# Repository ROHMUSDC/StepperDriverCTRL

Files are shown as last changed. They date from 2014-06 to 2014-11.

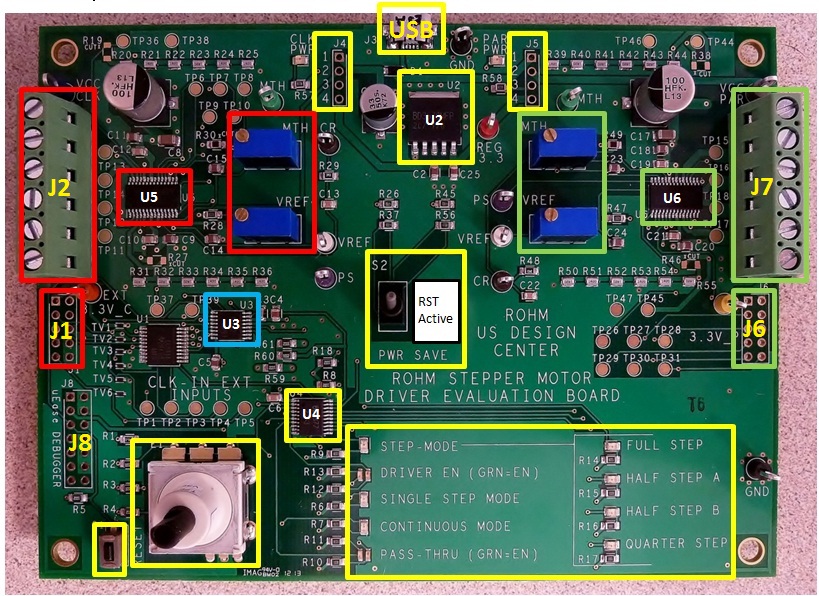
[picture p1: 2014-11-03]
raw images for manual/Fig 02 - Stepper Eval Board Diagram (labled).jpg

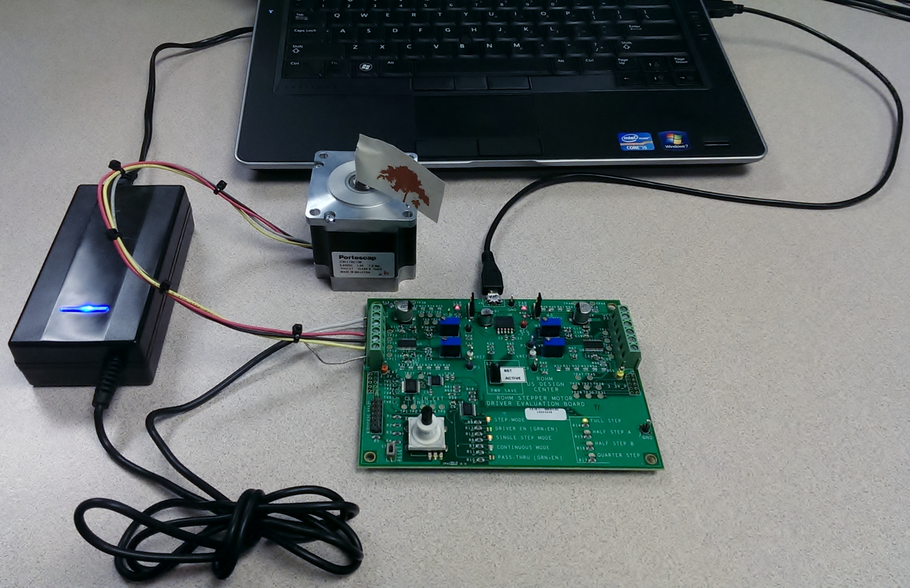
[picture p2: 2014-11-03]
raw images for manual/Fig 06 - Example Test Setup.jpg

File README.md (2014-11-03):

StepperDriverCTRL
=================

MCU: Lapis ML610Q102

The fully commented CONTROL firmware in this file is used to drive the ROHM BD63720EFV Stepper Motor Driver Eval Board. It is intended for reference. There are also many additional support files on this site. These support files for the for the Stepper Motor Eval Board include the Full User Manual a getting Started Flyer, Schematics, Bill of Material, etc.

This is the release version...but I do have plans to make future improvements...such as improving Continuous mode.

Evaluation Board Objective To allow customers and applications support the ability to evaluate any of Rohm’s BD637xx High Performance and BD638xx Micro Stepping Motor Drivers in a quick and easy environment. This document will describe the operation and functionality of the evaluation board.

Functionality The evaluation board has two drivers installed, the ROHM BD63720 Clock-in and the ROHM BD63876 Parallel input type. The BD63720 clock-driven High Performance Stepper Motor Driver is connected to an on-board LAPIS micro (ML610Q102) for demonstration purposes. Each circuit can also be connected to a user’s external MCU to control the driver and operate the attached stepper motor. Additionally, the ROHM BD63720 circuit can be controlled manually in a single step or continuous mode. The ROHM BD63720 and ROHM BD63876 are the 2A versions of each type. Users of lower current devices will be able to use these for evaluation as well.

Getting to know your Stepper Motor Eval Board • The RED Blocks in the Picture above highlight the key portions of the ROHM BD63720 Clock-in Stepper Motor Driver LSI (U5). The green terminal Block (J2) is where you will add Power for the Stepper Motor (i.e.: 24Vdc & GND), as well as where you will connect the 4 legs of the Bi Polar Stepper Motor windings if you want this IC to drive the Motor. This motor driver LSI is designed to be controlled via on-board pre-programmed Lapis ML610Q102 mcu (Blue Box above) (U3), or able to control via external mcu provided by the user (J1) • The Green Blocks in the Picture above highlight the key portions of the ROHM BD63876 Parallel-in Stepper Motor Driver LSI (U6). The green terminal Block (J7) is where you will add Power for the Stepper Motor (i.e.: 24Vdc & GND), as well as where you will connect the 4 legs of the Bi Polar Stepper Motor windings if you want this IC to drive the Motor. This motor driver LSI is designed to be controlled only via external mcu provided by the user (J6)

• The ROHM (SML-21 Series) LED’s in the lower corner of the board are controlled via a ROHM BD8377 12-ch. LED Driver (U4), and are used to indicate which Machine State the eval board in currently in in (adjustable via the push button encoder knob (E1)): o 4 possible Step Modes (Full, Half-A, Half-B or Quarter Step) o 2 possible Driver States (Disabled or Enabled) o 2 Possible Operation Modes (Single-Step or Continuous Mode) o 2 Possible Pass-Thru States (Disabled or Enabled)

• Suggested Motor o Portescap 23H118D10B Stepper Motor (1.8 Deg Step Angle; BiPolar) o Availible at DigiKey: http://www.digikey.com/product-detail/en/23H118D10B/403-1039-ND/1894182

• Key Potentiometer & Switch Settings o MTH => Current decay mode setting terminal (SLOW, MIXED or FAST Decay) o VREF => Output current value setting terminal o CR => Terminal to set the Chopping Frequency of output o PS => Power Save terminal - can put circuit in standby mode state and allow motor _ to operate o J4 & J5 => Both should jump pins 3 & 4 together to allow powering control circuitry (3.3V) on the eval board from the power provided in the USB connector (5V) which is regulated down to 3.3V via the ROHM BD3570HFP LDO Voltage Regulator (U2).

Evaluation Board Objective To allow customers and applications support the ability to evaluate any of Rohm’s BD63720 & BD63876 High Performance Stepping Motor Drivers in a quick and easy environment.

Functionality The evaluation board has two drivers installed, the BD63720 Clock-in and the BD63876 Parallel input type. Each circuit can be connected to a user’s MCU to control the driver and operate the attached stepper motor. Additionally, the BD63720 circuit can be controlled manually in a single step or continuous mode.

LED INDICATORS • Step Mode Indicates that the step modes can be selected by rotating the knob. o Full Step Indicates that the Full Step Mode has been selected for manual mode o Half Step A Indicates that the Half Step A Mode has been selected for manual mode. o Half Step B Indicates that the Half Step B Mode has been selected for manual mode. o Quarter Step Indicates that the Quarter Step Mode has been selected for manual mode. • Driver Enabled - RED Indicates that the Manual mode is ready but currently disabled • Driver Enabled - GREEN Indicates that the driver is now enabled for Manual mode • Single Step Mode Indicates that the board is prepared to operate in single step mode. • Continuous Indicates that the board is prepared to operate in continuous mode. • Pass Through - RED Indicates that the Pass-Through mode has been selected but disabled • Pass Through - GREEN Indicates that the Pass-Through mode is now enabled

KEY Components BD63720EFV - 36V Extra High-performance & High Reliability Stepper Motor Driver The BD63720EFV is a bipolar low-consumption driver that is driven by PWM current. Rated power supply voltage of the device is 36 V, and rated output current is 2.0A. CLK-IN driving mode is adopted for input interface, and excitation mode is corresponding to FULL STEP mode, HALF STEP mode (2 types) and QUARTER STEP mode via a built-in DAC. In terms of current decay, the FAST DECAY/SLOW DECAY ratio may be set without any limitation, and all available modes may be controlled in the most appropriate way. In addition, the power supply may be driven by one single system, which simplifies the design.

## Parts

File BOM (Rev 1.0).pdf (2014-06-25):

Stepper Motor Eval Board - B.O.M.

## ROHM Stepper Motor Driver Eval Board

Bill Of Materials
Item | Quantity | Reference | Package | Note | Value | Manufacturer | Manufacturer's Part No. | Digi-Key Part No. (with Hyperlinks)
1 | 10 | C2,C5,C9,C11,C14,C15,C18,C20,C23,C2 4 | SMD 0805 (2012 Metric) | Decoupling caps (100v) | 0.1µF | TDK Corporation | C2012X7R2A104K | 445-1418-1-ND (http://www.digikey.com/product-detail/en/C2012X7R2A104K/445-1418-1-ND/569084)
2 | 1 | C1 | Surface Mount "Cans"- (2-pads) | Vreg Input Aluminum Electrolytic Cap (50V) 20% | 33µF | Panasonic | EEE-1HA330XP | PCE3925CT-ND (http://www.digikey.com/product-detail/en/EEE-1HA330XP/PCE3925CT-ND/766301)
3 | 2 | C3,C6 | SMD 0805 (2012 Metric) | bypass caps | 0.01µF | TDK Corporation | C2012X7R2E103K | 445-2280-1-ND (http://www.digikey.com/product-detail/en/C2012X7R2E103K/445-2280-1-ND/789789)
4 | 2 | C4, C25 | SMD 0805 (2012 Metric) | filter cap | 4.7µF | TDK Corporation | C2012Y5V1A475Z/1.25 | 445-1370-1-ND (http://www.digikey.com/product-detail/en/C2012Y5V1A475Z%2F1.25/445-1370-1-ND/567609)
5 | 2 | C7,C16 | Surface Mount "Cans"- (2-pads) | filter caps - Aluminum Electrolytic Cap (50V) 20% | 100µF, 50V | Panasonic | EEE-FK1H101P | PCE3809CT-ND (http://www.digikey.com/product-detail/en/EEE-FK1H101P/PCE3809CT-ND/766185)
6 | 2 | C8,C17 | SMD 0805 (2012 Metric) | filter caps - Cer 1uF 100V 10% X7R 1206 | 1.0µF | Taiyo Yuden | HMK316B7105KL-T | 587-1777-1-ND (http://www.digikey.com/product-detail/en/HMK316B7105KL-T/587-1777-1-ND/1212793)
7 | 6 | C10,C12,C13,C19,C21,C22 | SMD 0805 (2012 Metric) | bypass caps | 0.001µF | TDK Corporation | C2012X7R2A102K | 45-1337-6-ND
8 | 3 | LED1, LED3, LED4 | SMD 0805 (2012 Metric) | MODE ("STEP; SINGLE; CONTINUOUS") LED Indicators | ORANGE LEDs | ROHM | SML-210DTT86 | 511-1284-6-ND
| 4 | LED6, LED7, LED8, LED9 | SMD 0805 (2012 Metric) | STEP ("FULL; HALF-A; HALF-B; QUARTER") LED Indicators | YELLOW LEDs | ROHM | SML-210YTT86 | 511-1290-6-ND
| 2 | LED10, LED11 | SMD 0805 (2012 Metric) | POWER ("CLK-PWR; PAR-PWR") LED Indicators | RED LEDs | ROHM | SML-210VTT86 | 511-1289-6-ND
9 | 2 | LED2, LED5 | Surface Mount - (4-pads) | Bi-Color LED's | Red/Green Bi-Color LED | ROHM | SML-521MUWT86 | 511-1317-6-ND (http://www.digikey.com/product-detail/en/SML-521MUWT86/511-1317-6-ND/1800424)
10 | 1 | E1 | Through-hole (5-pins + 3 mounting tabs) | Encoder with Push Button | Encoder with Push Button | Grayhill | 62P22-L6 | GH7296-ND (http://www.digikey.com/scripts/DkSearch/dksus.dll?WT.z_header=search_go&lang=en&x=0&y=0&cur=USD)
11 | 1 | J3 | SMD micro USB | micro USB for Power Source | microUSB | Hirose Electric Co Ltd | ZX62R-B-5P | H11574CT-ND (http://www.digikey.com/product-detail/en/ZX62R-B-5P/H11574CT-ND/1787106)
12 | 2 | J2, J7 | Through-hole (6-pin ) | 16A, 300V Output Screw Terminal Blocks (1x6) | 1x6 pins | FCI | 20020316-G061B01LF | 609-3931-ND (http://www.digikey.com/scripts/DkSearch/dksus.dll?WT.z_header=search_go&lang=en&x=0&y=0&cur=USD)
13 | 2 | J4, J5 | Through-hole (4-pin ) | Pwr Source Selector (1x4) | 1x4 pins | Molex Inc | 901200124 | WM8074-ND (http://www.digikey.com/scripts/DkSearch/dksus.dll?WT.z_header=search_go&lang=en&x=0&y=0&cur=USD)
14 | 2 | J1, J6 | Through-hole (10-pin ) | External Input Headers (5x2) | 5x2 pins (gold) | Samtec Inc | TSW-150-07-L-D | SAM1030-50-ND (http://www.digikey.com/scripts/DkSearch/dksus.dll?WT.z_header=search_go&lang=en&x=0&y=0&cur=USD)
15 | 1 | J8 | Through-hole (14-pin ) | 14-Pin Debugger Header (7x2) | 7x2 pins (gold) | Samtec Inc | TSW-150-07-L-D | SAM1030-50-ND (http://www.digikey.com/scripts/DkSearch/dksus.dll?WT.z_header=search_go&lang=en&x=0&y=0&cur=USD)
16 | 4 | POT1,POT2,POT3,POT4 | Through-hole (3-pin ) | 21-Turn 10K Trimmer Pot. (Through-hole) | 10kΩ potentiometers | Vishay Sfernice | T93YB103KT20 | T93YB-10K-ND (http://www.digikey.com/scripts/DkSearch/dksus.dll?WT.z_header=search_go&lang=en&x=0&y=0&cur=USD)
17 | 1 | R1 | SMD 0805 (2012 Metric) | RES 91.0 OHM 1/8W 1% 0805 SMD | 91Ω | ROHM | MCR10EZPF91R0 | RHM91.0CRCT-ND (http://www.digikey.com/product-detail/en/MCR10EZPF91R0/RHM91.0CRCT-ND/1214413)
18 | 9 | R2,R3,R4,R5,R8,R18,R59,R60,R61 | SMD 0805 (2012 Metric) | RES 10.0K OHM 1/8W 1% 0805 SMD | 10kΩ | ROHM | MCR10EZPF1002 | RHM10.0KCRCT-ND (http://www.digikey.com/product-detail/en/MCR10EZPF1002/RHM10.0KCRCT-ND/1214072)
19 | 15 | R6,R7,R9,R10,R11,R12,R13,R14,R15,R 16,R17,R28,R47, R57, R58 | SMD 0805 (2012 Metric) | RES 1.00K OHM 1/8W 1% 0805 SMD | 1kΩ | ROHM | MCR10EZPF1001 | RHM1.00KCRCT-ND (http://www.digikey.com/product-detail/en/MCR10EZPF1001/RHM1.00KCRCT-ND/1214071)
20 | 4 | R19,R27,R38,R46 | SMD 0805 (2012 Metric) | 0-Ohm jumper resistors | 0Ω | ROHM | MCR10EZPJ000 | RHM0.0ARCT-ND (http://www.digikey.com/product-detail/en/MCR10EZPJ000/RHM0.0ARCT-ND/1214418)
21 | 24 | R20,R21,R22,R23,R24,R25,R31,R32,R3 3,R34,R35,R36,R39,R40,R41,R42,R43, R44,R50,R51,R52,R53,R54,R55 | SMD 0805 (2012 Metric) (Wide) | RES 1.20 OHM 1/2W 1% 2012 WIDE | 1.2Ω | ROHM | LTR10EVHFL1R20 | RHM1.20BSCT-ND (http://www.digikey.com/product-detail/en/LTR10EVHFL1R20/RHM1.20BSCT-ND/2708172)
22 | 4 | R26,R37,R45,R56 | SMD 0805 (2012 Metric) | RES 4.70K OHM 1/8W 1% 0805 SMD | 4.7kΩ | ROHM | MCR10EZPF4701 | RHM4.70KCRCT-ND (http://www.digikey.com/product-detail/en/MCR10EZPF4701/RHM4.70KCRCT-ND/1214304)
23 | 2 | R29,R48 | SMD 0805 (2012 Metric) | RES 39.0K OHM 1/8W 1% 0805 SMD | 39kΩ | ROHM | MCR10EZHF3902 | RHM39.0KCCT-ND (http://www.digikey.com/product-detail/en/MCR10EZHF3902/RHM39.0KCCT-ND/629446)
24 | 2 | R30,R49 | SMD 0805 (2012 Metric) | RES 3.48K OHM 1/8W 1% 0805 SMD | 3.48kΩ | ROHM | TRR10EZPF3481 | RHM3.48KCRCT-ND (http://www.digikey.com/product-detail/en/MCR10EZPF3481/RHM3.48KCRCT-ND/1214247)
25 | 1 | S1 | Surface Mount (2-pad) | Micro's Reset Button | Momentary Push-Button (NO) | E-Switch | TL3302AF180QG | EG2528DKR-ND
26 | 1 | S2 | Through-hole (6-pin ) | Stepper Driver PowerSave Toggle Switch | DPDT Switch | NKK Switches | G22AP | G22AP-ND (http://www.digikey.com/scripts/DkSearch/dksus.dll?WT.z_header=search_go&lang=en&x=0&y=0&cur=USD)
27 | 1 | TP19 | Through-hole (1-pin ) | Test Point, RED Keystone 5010 | Reg_+3.3V | Keystone | 5010 | 5010K-ND (http://www.digikey.com/product-search/en/test-and-measurement/test-points/2294346?k=5010K-ND)
28 | 1 | TP20 | Through-hole (1-pin ) | Test Point, ORANGE Keystone 5013 | Ext_+3.3V_C | Keystone | 5013 | 5013K-ND (http://www.digikey.com/scripts/DkSearch/dksus.dll?WT.z_header=search_go&lang=en&x=0&y=0&cur=USD)
29 | 1 | TP21 | Through-hole (1-pin ) | Test Point, YELLOW Keystone 5014 | Ext_+3.3V_P | Keystone | 5014 | 5014K-ND (http://www.digikey.com/scripts/DkSearch/dksus.dll?WT.z_header=search_go&lang=en&x=0&y=0&cur=USD)
30 | 1 | TP22 | Through-hole (1-pin ) | Test Point, BLUE Keystone 5127 | VCC_C | Keystone | 5027 | 5127K-ND (http://www.digikey.com/product-search/en/test-and-measurement/test-points/2294346?k=5127K-ND)
31 | 1 | TP23 | Through-hole (1-pin ) | Test Point, GREY Keystone 5128 | VCC_P | Keystone | 5028 | 5128K-ND (http://www.digikey.com/product-search/en/test-and-measurement/test-points/2294346?k=5128K-ND)
32 | 1 | TP24 | Through-hole (1-pin ) | Test Point, BLACK Keystone 5011 | GND | Keystone | 5011 | 5011K-ND (http://www.digikey.com/scripts/DkSearch/dksus.dll?WT.z_header=search_go&lang=en&x=0&y=0&cur=USD)
33 | 1 | TP25 | Through-hole (1-pin ) | Test Point, BLACK Keystone 5011 | GND | Keystone | 5011 | 5011K-ND (http://www.digikey.com/scripts/DkSearch/dksus.dll?WT.z_header=search_go&lang=en&x=0&y=0&cur=USD)
34 | 1 | TP33 | Through-hole (1-pin ) | Test Point, WHITE Keystone 5012 | Clk_VREF | Keystone | 5012 | 5012K-ND (http://www.digikey.com/scripts/DkSearch/dksus.dll?WT.z_header=search_go&lang=en&x=0&y=0&cur=USD)
35 | 1 | TP41 | Through-hole (1-pin ) | Test Point, WHITE Keystone 5012 | Par_VREF | Keystone | 5012 | 5012K-ND (http://www.digikey.com/scripts/DkSearch/dksus.dll?WT.z_header=search_go&lang=en&x=0&y=0&cur=USD)
36 | 1 | TP42 | Through-hole (1-pin ) | Test Point, BROWN Keystone 5125 | Par_CR | Keystone | 5025 | 5125K-ND (http://www.digikey.com/product-search/en/test-and-measurement/test-points/2294346?k=5125K-ND)
37 | 1 | TP34 | Through-hole (1-pin ) | Test Point, BROWN Keystone 5125 | Clk_CR | Keystone | 5025 | 5125K-ND (http://www.digikey.com/product-search/en/test-and-measurement/test-points/2294346?k=5125K-ND)
38 | 1 | TP35 | Through-hole (1-pin ) | Test Point, GREEN Keystone 5126 | Clk_MTH | Keystone | 5026 | 5126K-ND (http://www.digikey.com/product-search/en/test-and-measurement/test-points/2294346?k=5126K-ND)
39 | 1 | TP43 | Through-hole (1-pin ) | Test Point, GREEN Keystone 5126 | Par_MTH | Keystone | 5026 | 5126K-ND (http://www.digikey.com/product-search/en/test-and-measurement/test-points/2294346?k=5126K-ND)
40 | 1 | TP32 | Through-hole (1-pin ) | Test Point, PURPLE Keystone 5129 | Clk_PS | Keystone | 5029 | 5129K-ND (http://www.digikey.com/product-search/en/test-and-measurement/test-points/2294346?k=5129K-ND)
41 | 1 | TP40 | Through-hole (1-pin ) | Test Point, PURPLE Keystone 5129 | Par_PS | Keystone | 5029 | 5129K-ND (http://www.digikey.com/product-search/en/test-and-measurement/test-points/2294346?k=5129K-ND)
42 | 1 | U1 | Surface Mount - TSSOP (20-pin) | Octal Buffer IC BUFF/DVR TRI-ST 8BIT 20SSOP | 74LVC541A | Texas Instruments | SN74LVC541ADBR | 296-8518-1-ND (http://www.digikey.com/product-detail/en/SN74LVC541ADBR/296-8518-1-ND/377508)
43 | 6 | TV1, TV2, TV3, TV4, TV5, TV6 | Surface Mount - VMD2 (2 Pads) | ZENER ESD Protection Diodes - 10W VMD2 | 5.78V 100mW | ROHM | RSB6.8GT2R | RSB6.8GT2RCT-ND (http://www.digikey.com/product-detail/en/RSB6.8GT2R/RSB6.8GT2RCT-ND/669851)
44 | 1 | D1 | Surface Mount - 123SOD (2-pads) | Schottkey Diode Input Protection - 20V 3A 123-SOD | 20V 3A | ROHM | RB051M-2YTR | RB051M-2YCT-ND (http://www.digikey.com/product-detail/en/RB051M-2YTR/RB051M-2YCT-ND/2615726)
45 | 1 | U2 | Surface Mount - HRP5 (5-pins plus tab) | 3.3v LDO Reg (USB 5V to 3.3v, etc) | 3.3V Reg | ROHM | BD3570HFP | ROHM-SAMPLES
46 | 1 | U3 | Surface Mount - SSOP-16 (16-pin) | 5V, 8-Bit, 16-pin LAPIS Micro | 8-Bit Microcontroller | ROHM | ML610Q102 | ROHM-SAMPLES
47 | 1 | U4 | Surface Mount - SSOP-B20 (20-pin) | 12-Ch. LED Driver | LED Driver | ROHM | BD8377EFV | ROHM-SAMPLES
48 | 1 | U5 | Surface Mount - HTSSOP-B28 (28-pin + thermal pad) | Clock-In Stepper Motor Driver (28V 2.0A 28-HTSSOP) | Stepper Motor Driver (CLK) | ROHM | BD63720EFV | ROHM-SAMPLES
49 | 1 | U6 | Surface Mount - HTSSOP-B28 (28-pin + thermal pad) | Parallel-In Stepper Motor Driver | Stepper Motor Driver (PAR) | ROHM | BD63876EFV | ROHM-SAMPLES

Last Updated: 6/20/2014

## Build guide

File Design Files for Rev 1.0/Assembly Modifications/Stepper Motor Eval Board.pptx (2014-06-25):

## Stepper Motor Eval Board

Assembly Requests
Any questions, please feel free to contact Carl Schell at: cell: 313.414.6481

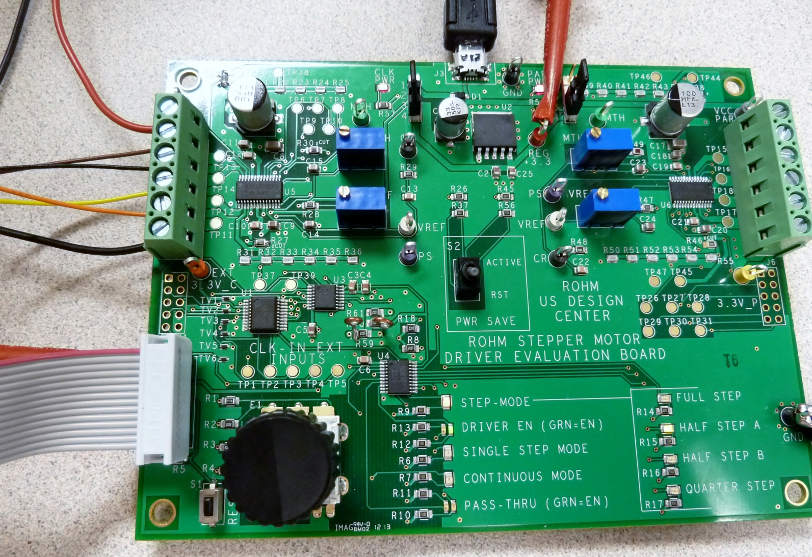
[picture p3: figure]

## Request Overview

1. Cut Trace at two points on bottom of PCB
2. Add jumper to top of PCB
3. Place components R19, R27, R38 & R46 (Previously listed as Do Not Populate). I will order these components today and provide them to you later this week. The only issue I see on this from your side is that your previous stencil was not cut for these 4 components…so this may require a new stencil??
4. The test points were placed correctly, but not oriented correctly (I had requested perpendicular to the edge of the board). I’m not sure if this is possible, but I will modify 1 of the 4 boards you provided me and provide it to you as a template of what I prefer. If not feasible, I will accept it as is.
5. The labels on the silkscreen at S2 are reversed from what I would like. I would like to see if you could make or order and place a nice sticker on the board near the switch to correct this.

## Request #1

- Cut Trace at two points on bottom of PCB

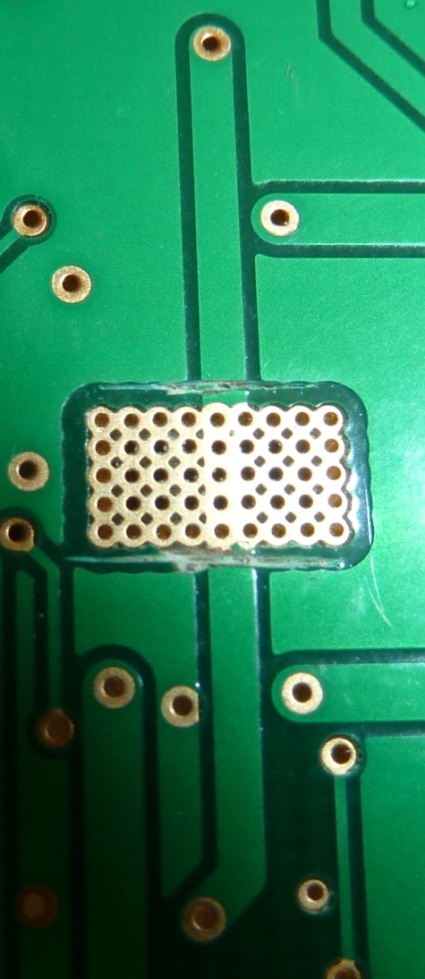
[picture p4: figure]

Bottom Side of PCB

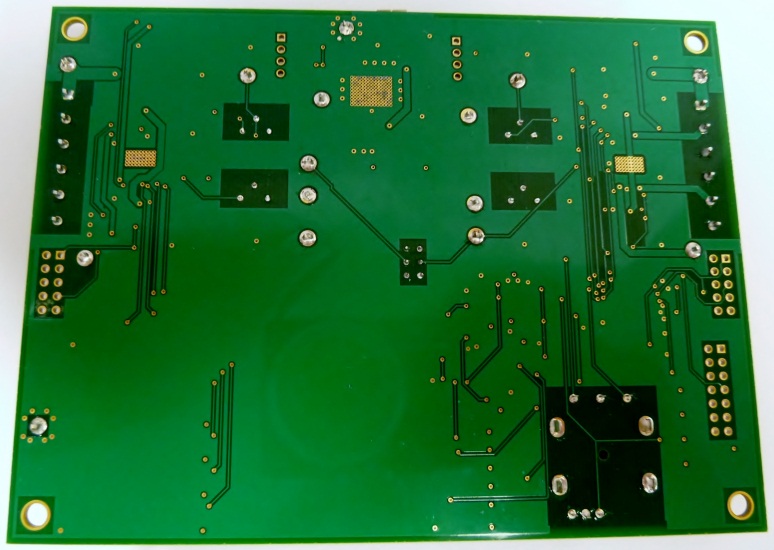
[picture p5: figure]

Sever the trace at two points

## Request #2

- Add jumper to bottom (preferred) or on top, if bottom is not feasible

Bottom Side of PCB

Top Side of PCB

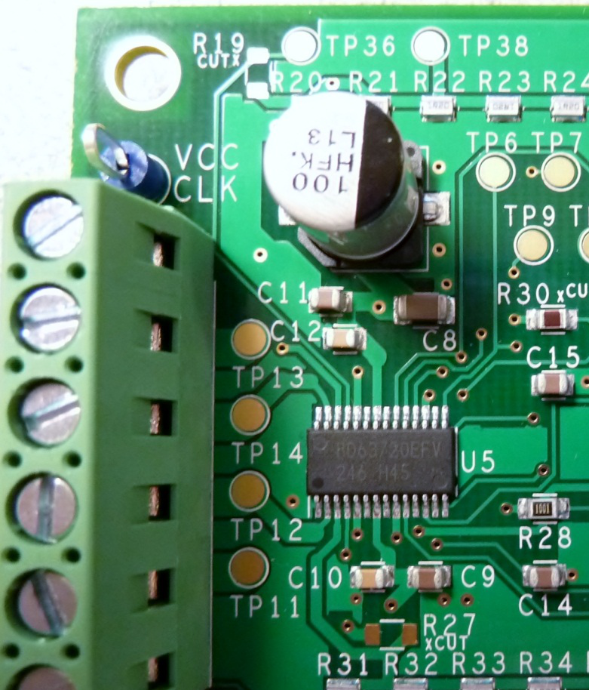
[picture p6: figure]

PREFFERED METHOD!

Or…

PREFFERED METHOD!

## Request #3

- Place components R19, R27, R38 & R46 (Previously listed as Do Not Populate).

Place (0Ω Jumpers) at: R19, R27, R38, R46

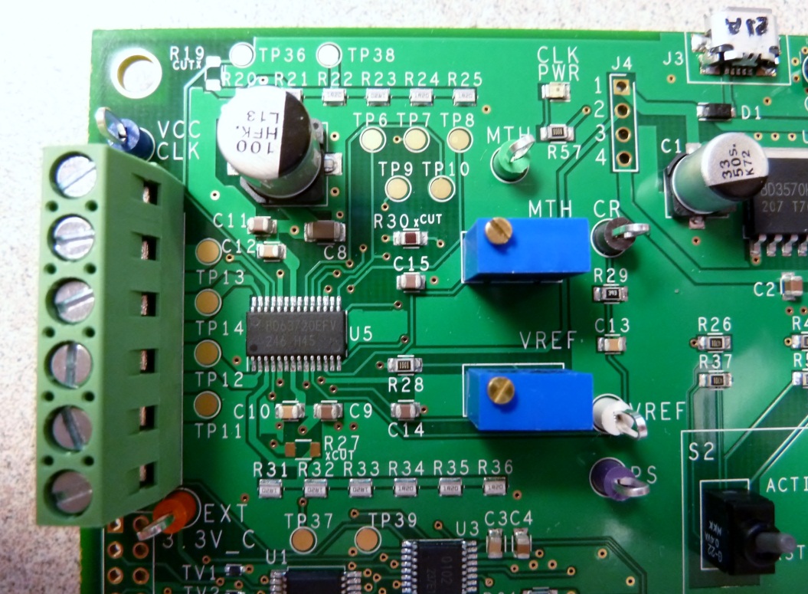
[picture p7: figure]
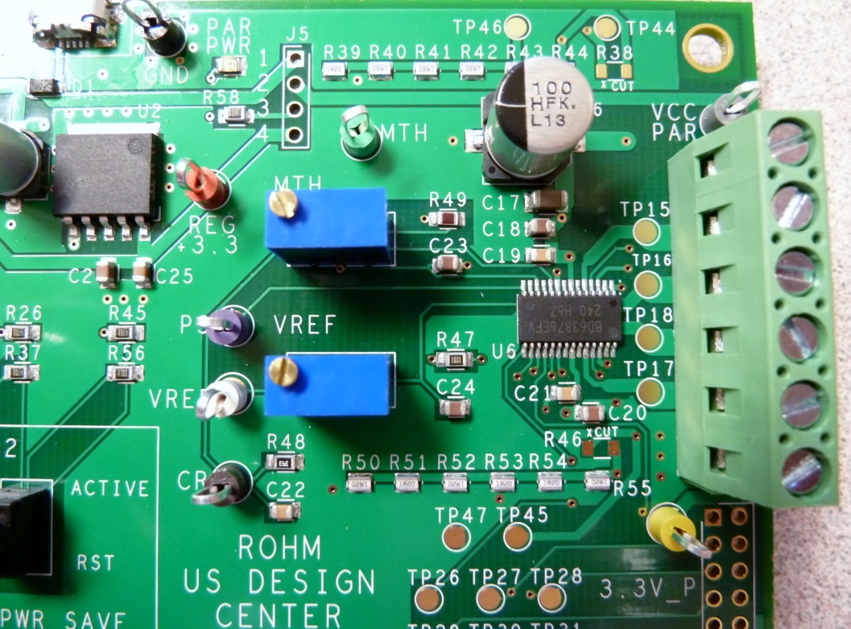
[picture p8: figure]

## Request #4

- Preferred Test Point Orientation is Perpendicular to the edge of the PCB…

Perfect – exactly as desired!

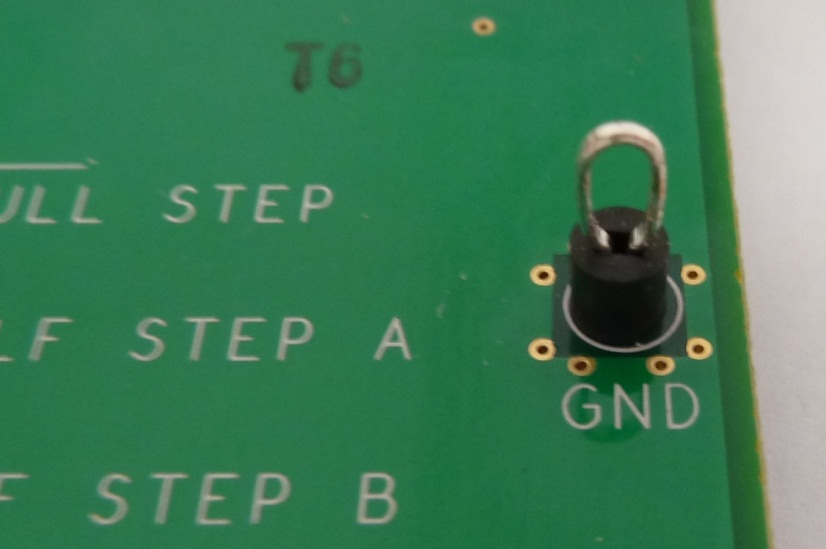
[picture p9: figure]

This test point’s orientation is not ideal...

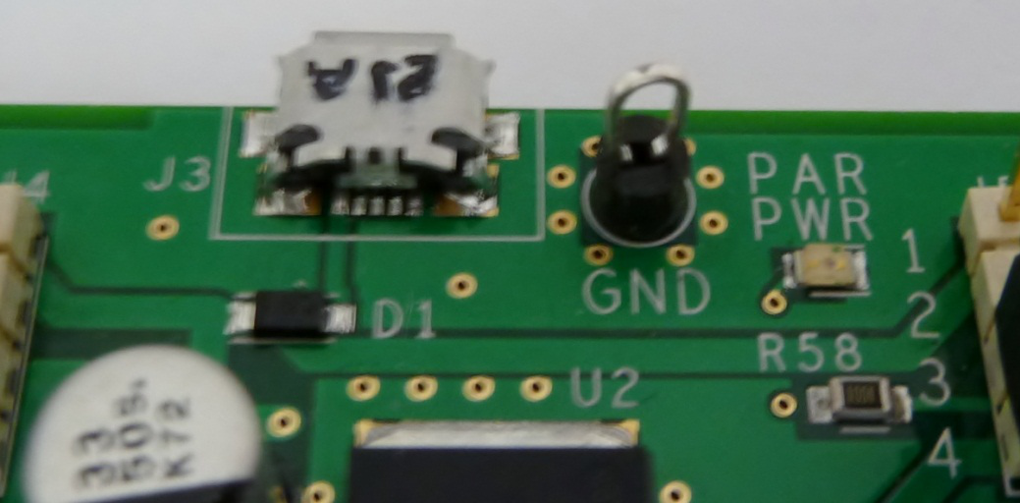
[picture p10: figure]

## Request #5

- Add Sticker to correct mislabeled Silkscreen…

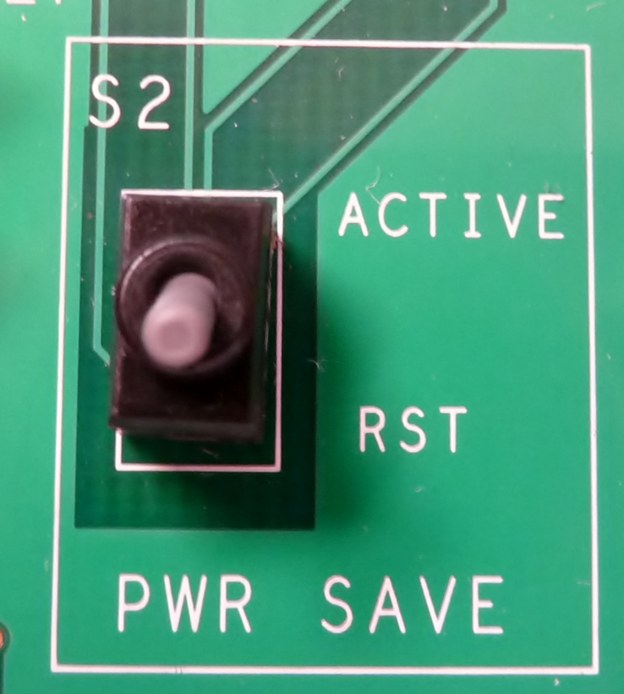
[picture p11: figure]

Something like this…

RST

ACTIVE

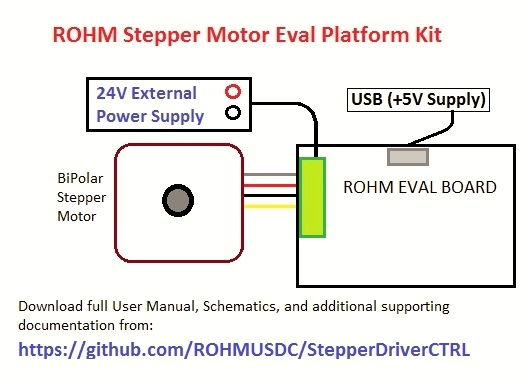
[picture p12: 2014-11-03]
Getting Started.jpg

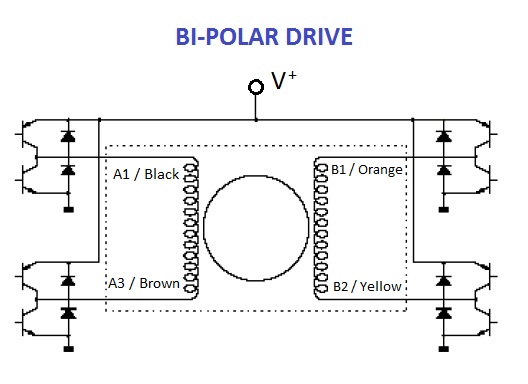
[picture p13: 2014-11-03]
raw images for manual/Fig 08 - BiPolar Drive Diagram.jpg

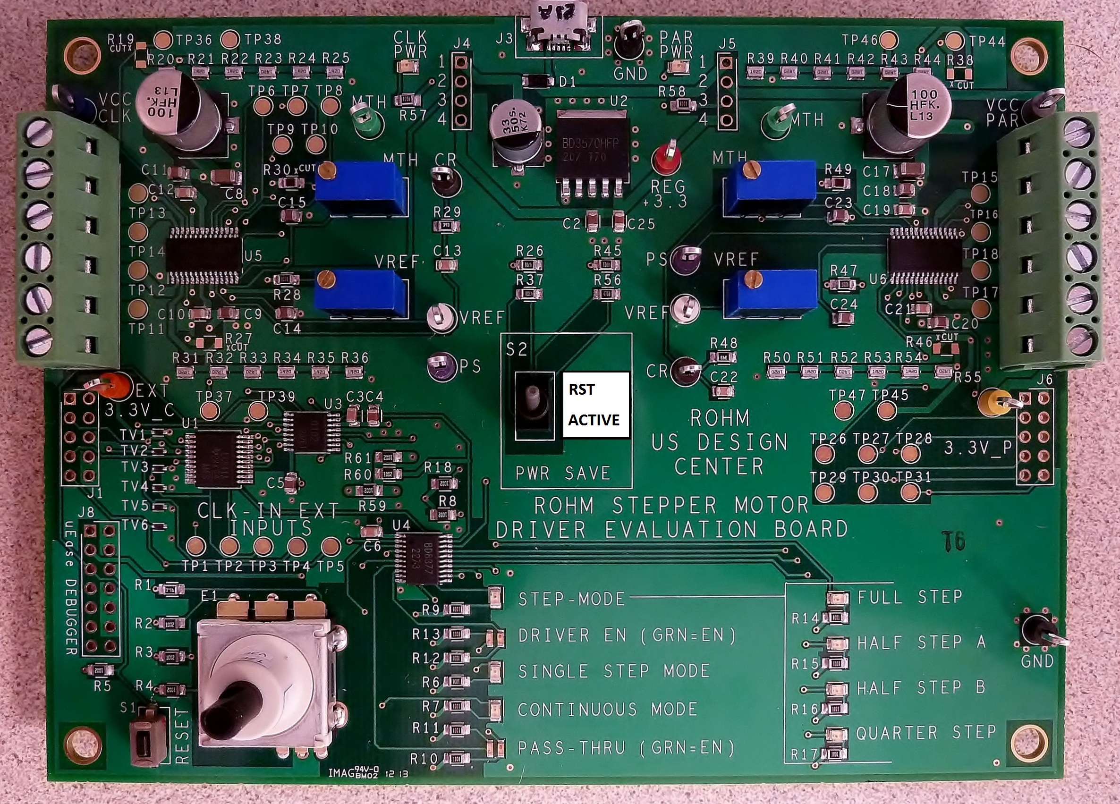
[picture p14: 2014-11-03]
raw images for manual/Fig 01 - Stepper Motor Eval Board.JPG

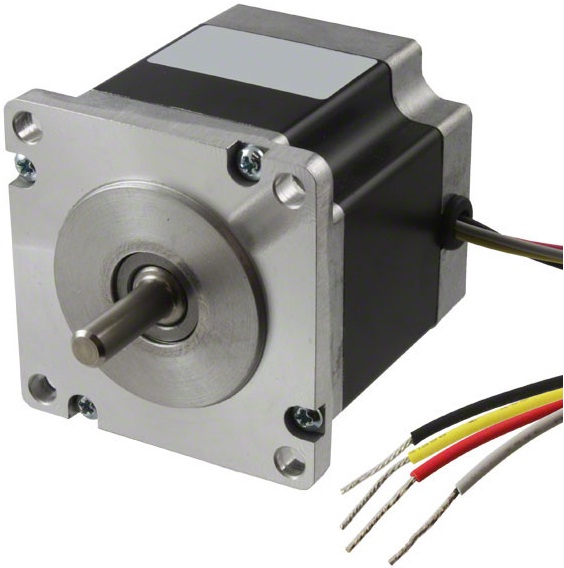
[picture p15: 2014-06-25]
raw images for manual/Fig 03 - Portescap 23H118D10B Stepper Motor.jpg

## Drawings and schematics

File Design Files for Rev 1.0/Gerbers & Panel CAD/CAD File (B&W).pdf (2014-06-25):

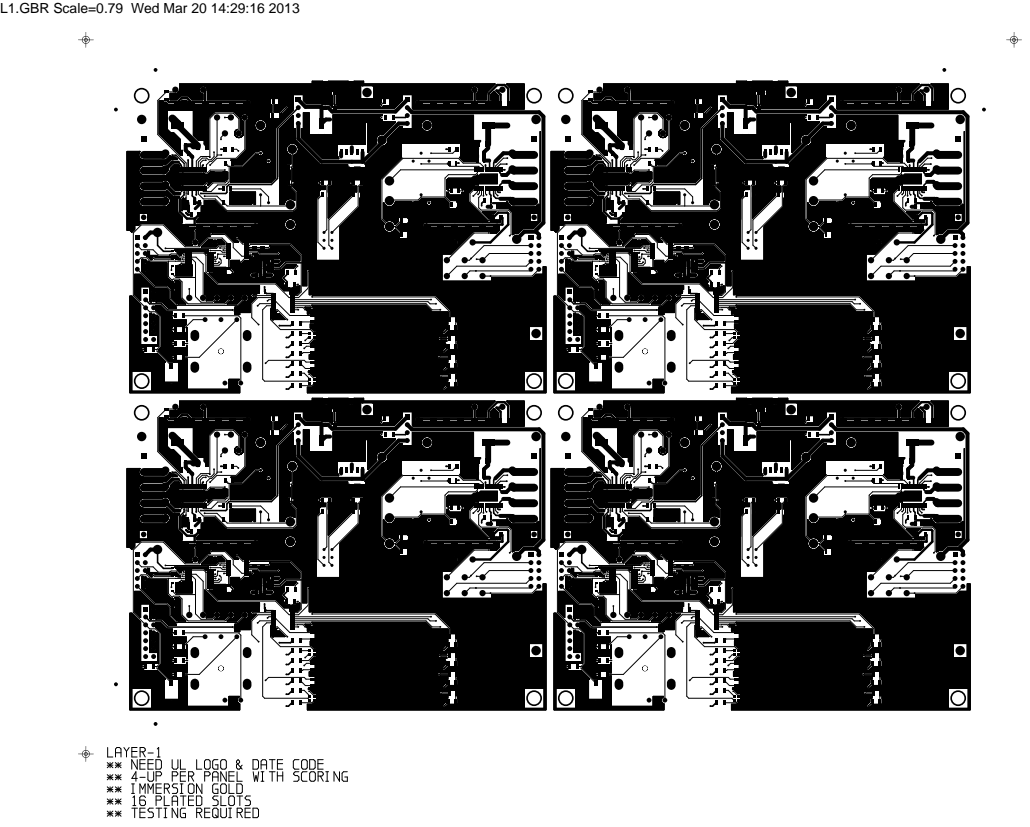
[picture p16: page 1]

L1.GBR Scale=0.79 Wed Mar 20 14:29:16 2013

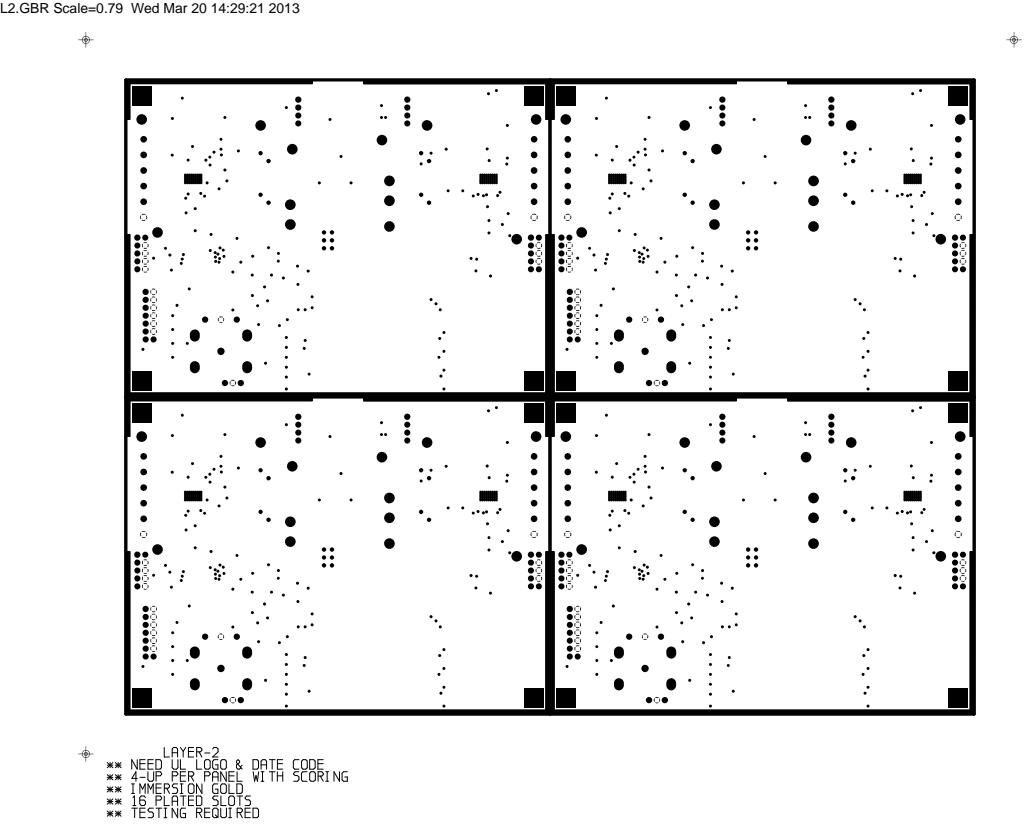
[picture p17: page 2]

L2.GBR Scale=0.79 Wed Mar 20 14:29:21 2013

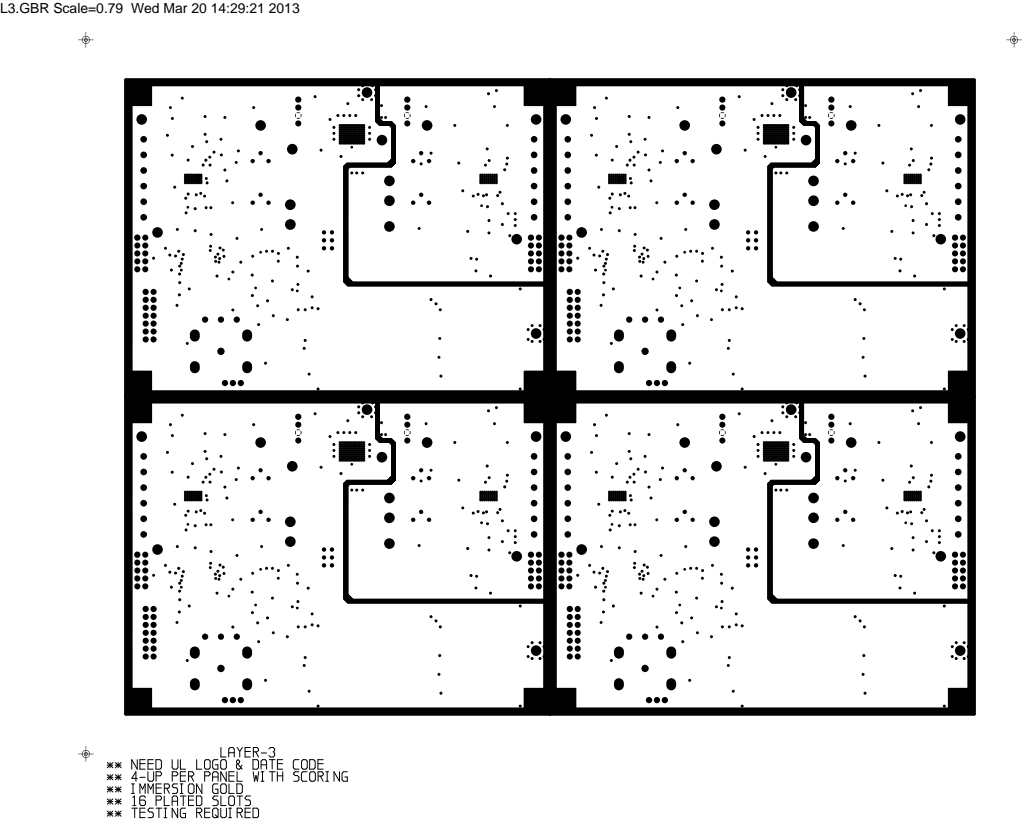
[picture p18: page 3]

L3.GBR Scale=0.79 Wed Mar 20 14:29:21 2013

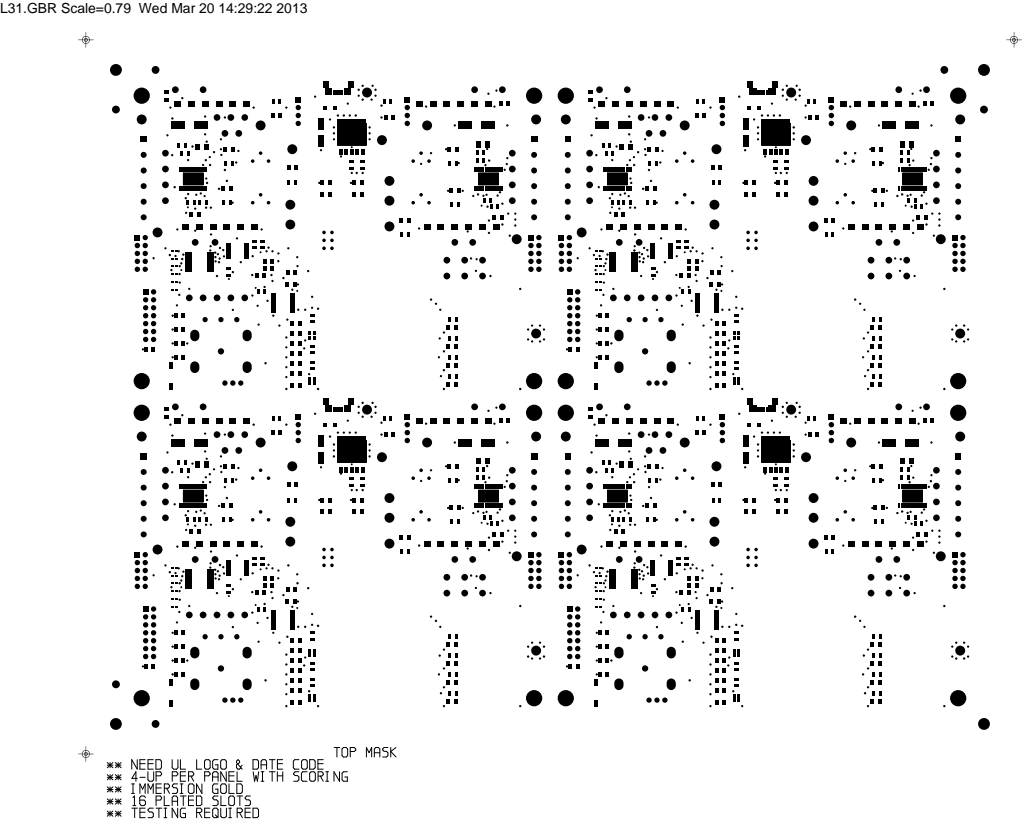
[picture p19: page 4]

L31.GBR Scale=0.79 Wed Mar 20 14:29:22 2013

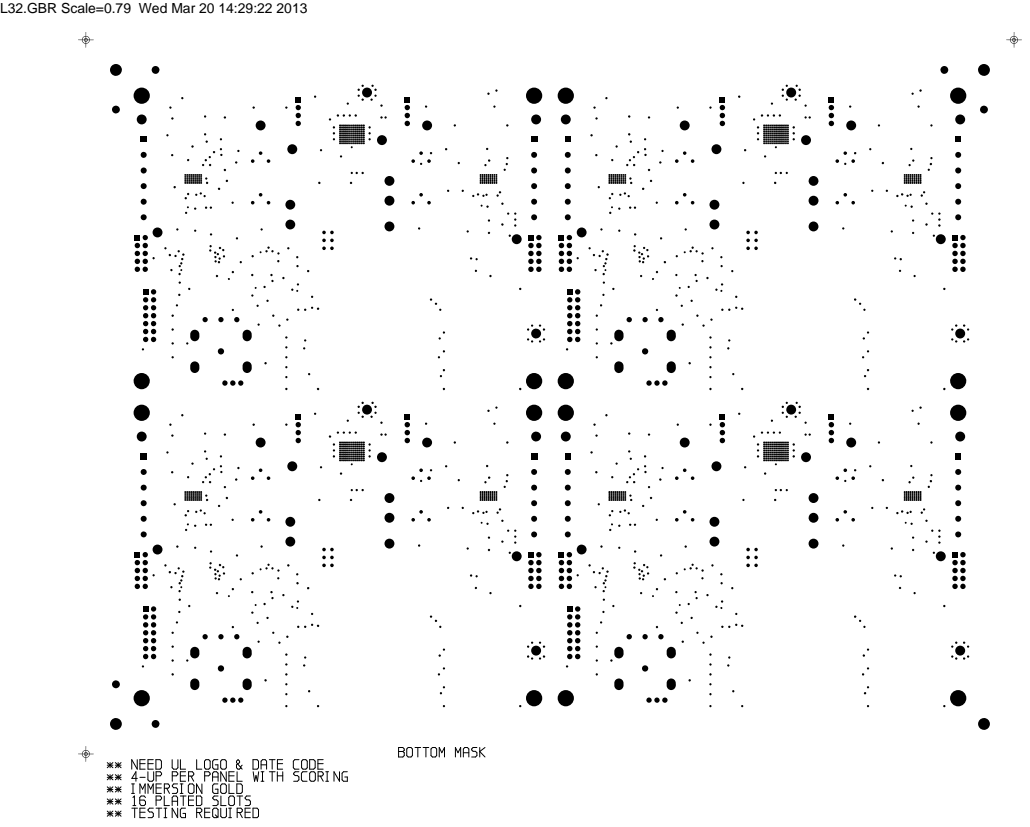
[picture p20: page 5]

L32.GBR Scale=0.79 Wed Mar 20 14:29:22 2013

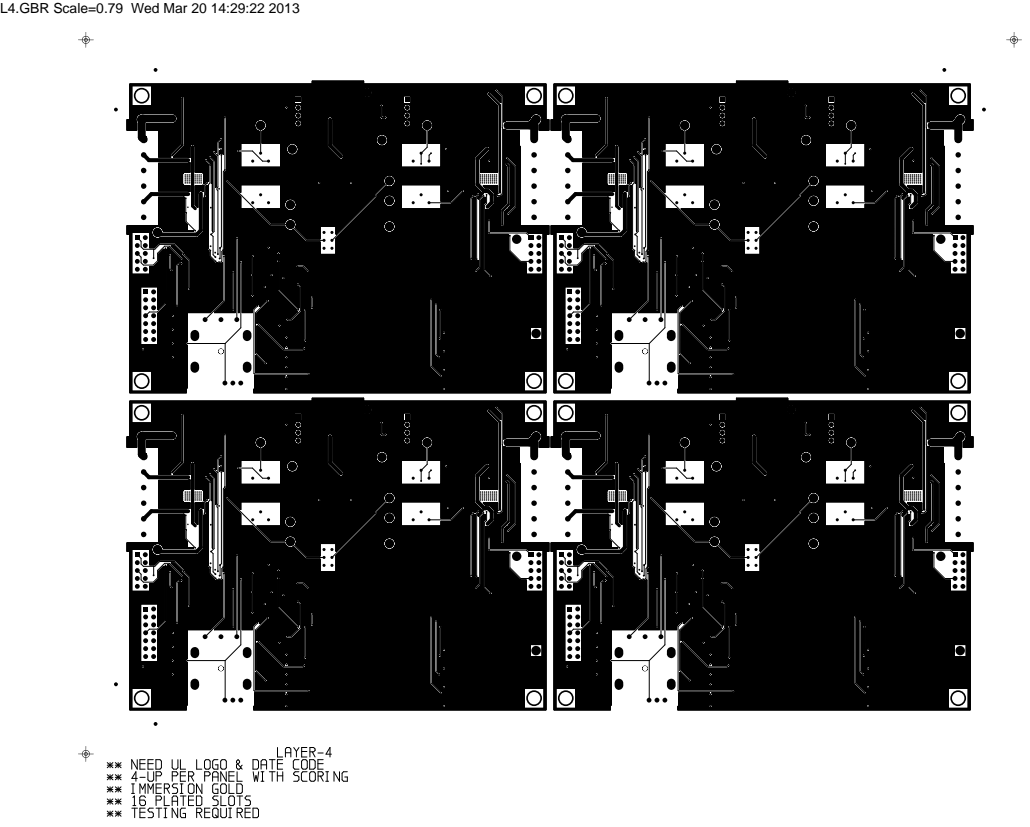
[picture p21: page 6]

L4.GBR Scale=0.79 Wed Mar 20 14:29:22 2013

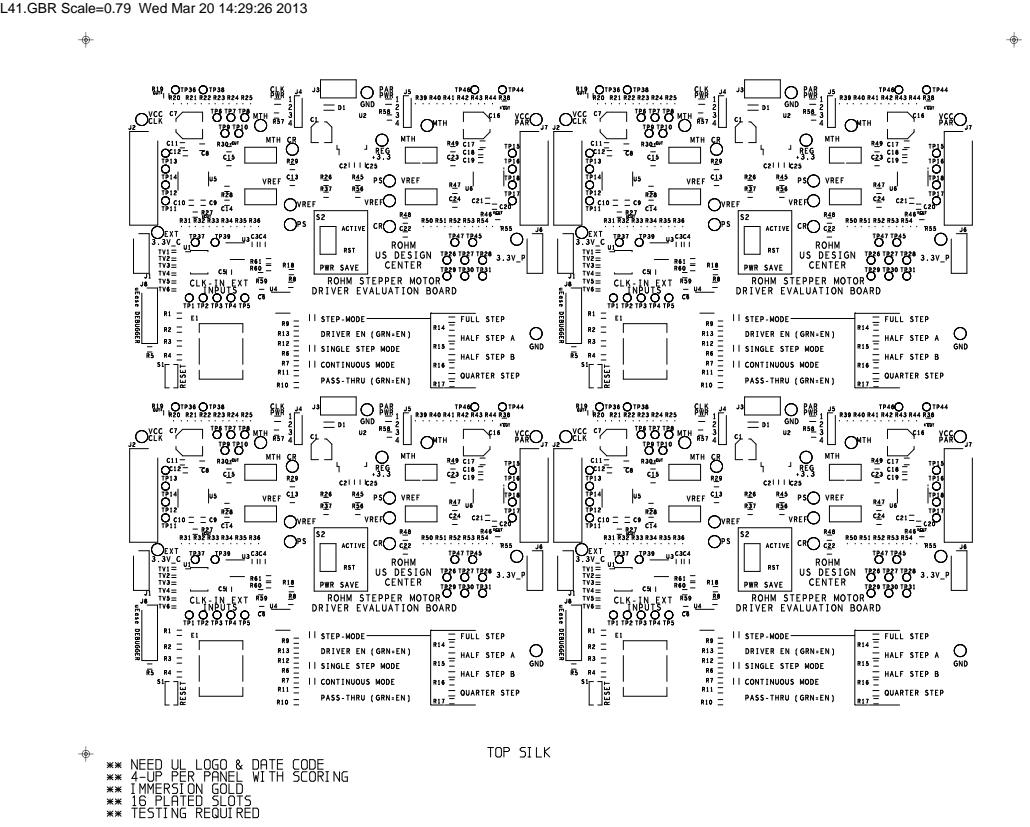
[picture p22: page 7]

L41.GBR Scale=0.79 Wed Mar 20 14:29:26 2013

L60.GBR Scale=0.79 Wed Mar 20 14:29:36 2013

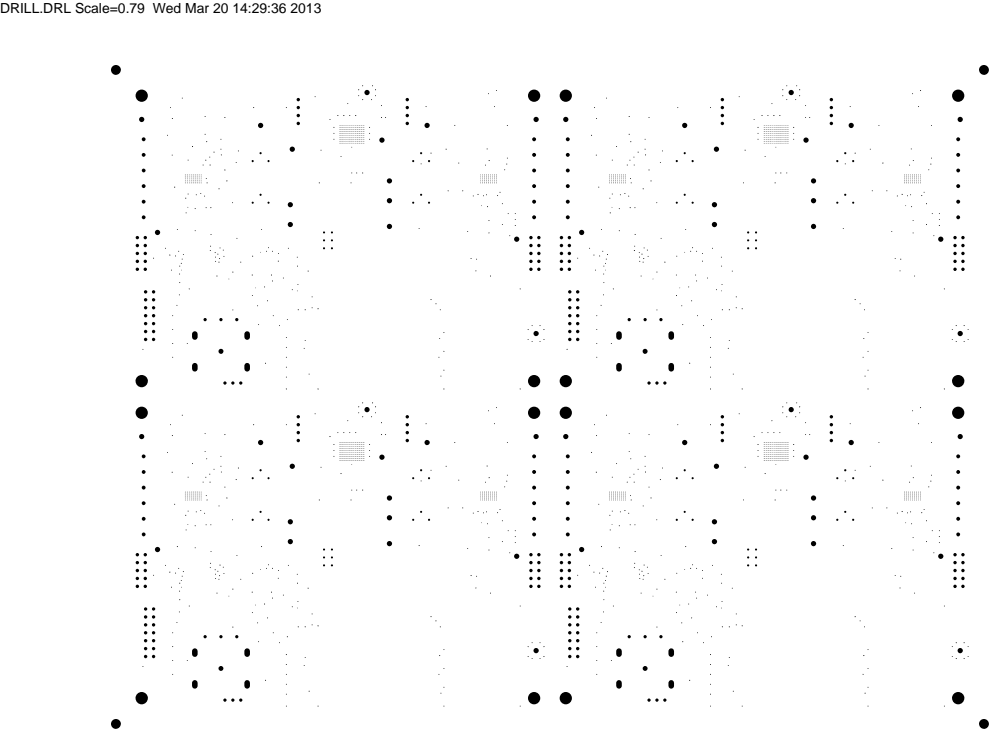
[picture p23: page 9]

DRILL.DRL Scale=0.79 Wed Mar 20 14:29:36 2013

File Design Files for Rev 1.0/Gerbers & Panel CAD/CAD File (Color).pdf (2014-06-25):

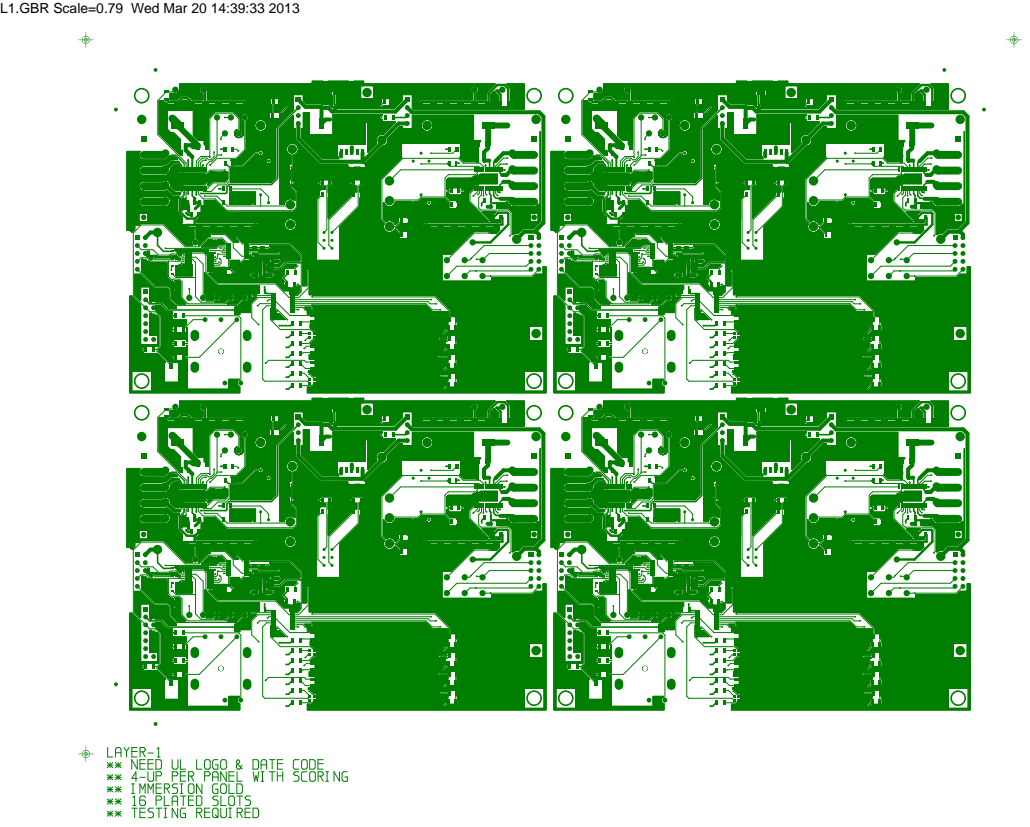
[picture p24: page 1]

L1.GBR Scale=0.79 Wed Mar 20 14:39:33 2013

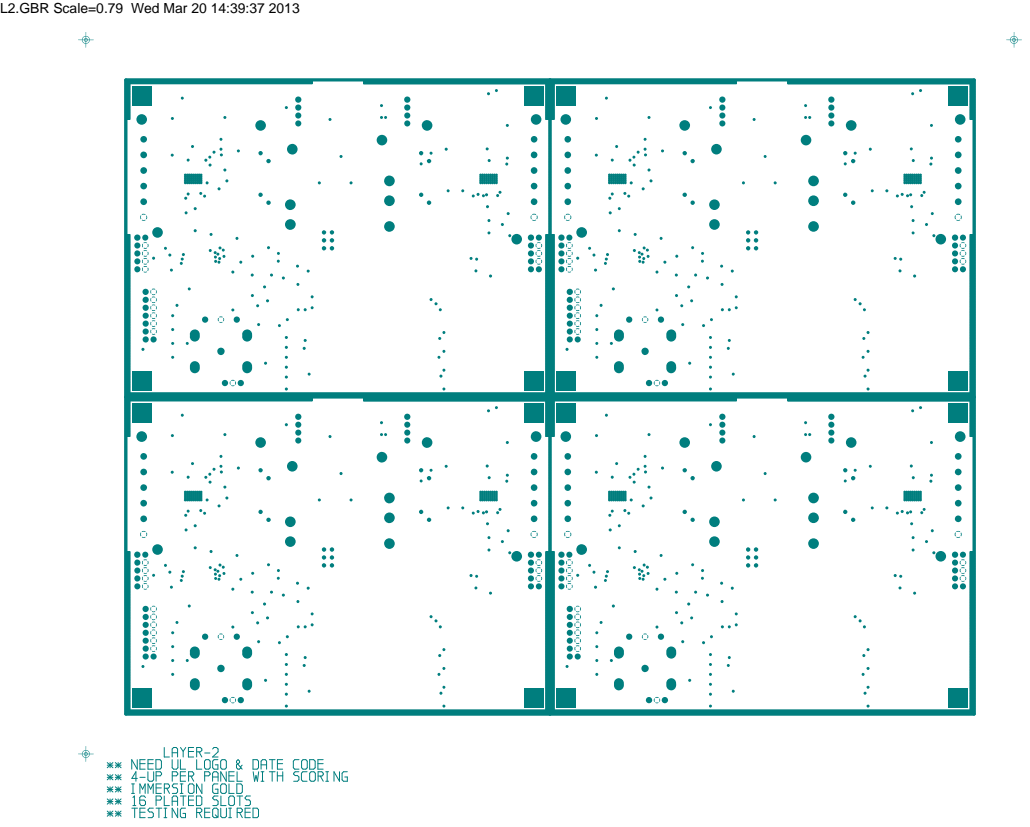
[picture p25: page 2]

L2.GBR Scale=0.79 Wed Mar 20 14:39:37 2013

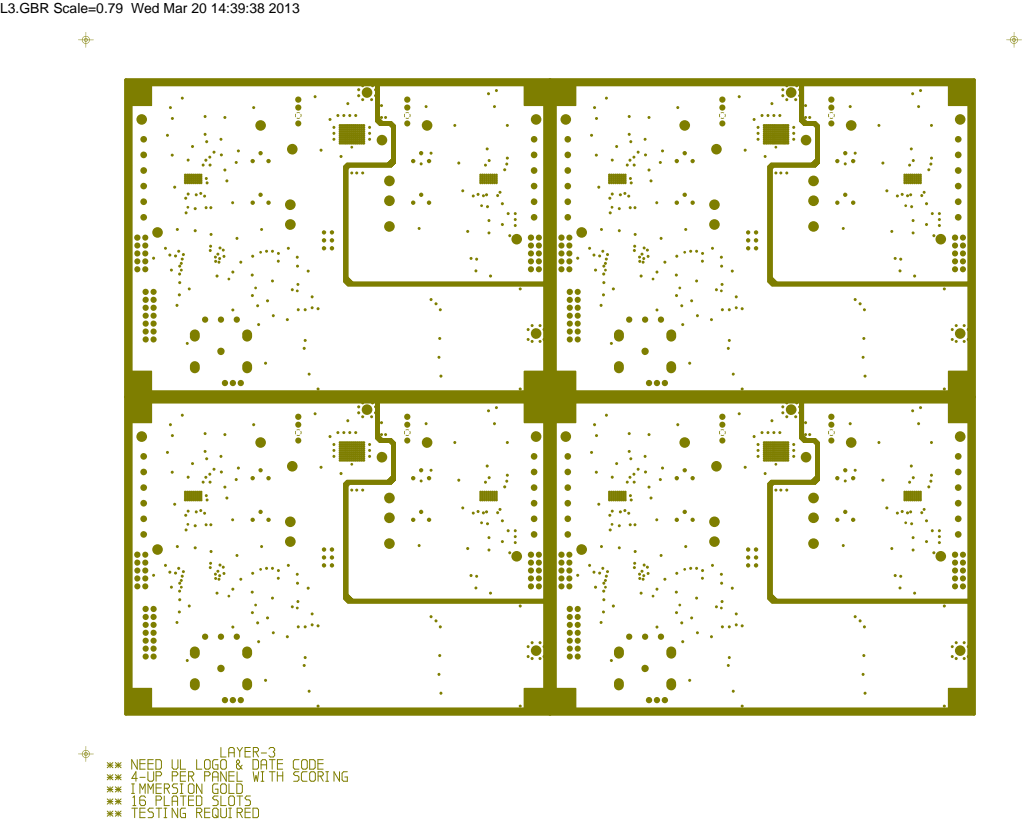
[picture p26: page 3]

L3.GBR Scale=0.79 Wed Mar 20 14:39:38 2013

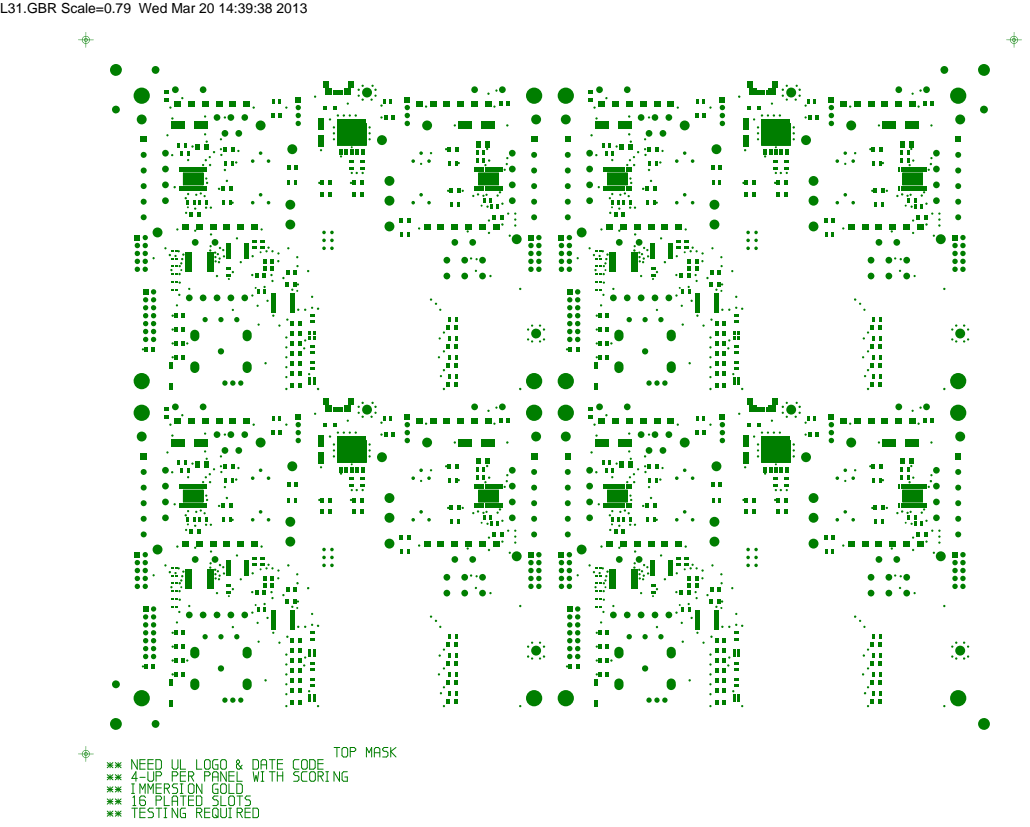
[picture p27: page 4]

L31.GBR Scale=0.79 Wed Mar 20 14:39:38 2013


L32.GBR Scale=0.79 Wed Mar 20 14:39:39 2013


L4.GBR Scale=0.79 Wed Mar 20 14:39:39 2013


L41.GBR Scale=0.79 Wed Mar 20 14:39:42 2013

L60.GBR Scale=0.79 Wed Mar 20 14:39:53 2013


DRILL.DRL Scale=0.79 Wed Mar 20 14:39:53 2013

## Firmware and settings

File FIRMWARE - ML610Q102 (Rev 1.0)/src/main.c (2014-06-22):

//*****************************************************************************
// Program:	 Stepper Motor Driver IC Evaluation Board Controller (ML610Q102)
//		
// Author:	 C. Schell
//		 	ROHM Semiconductor USA, LLC
//			 US Design Center
// Started:  June 19th, 2013
// Purpose:	 Demonstration Code for use with Stepper Motor Driver Board
//
// Code Status:	Released Version - Working Well
//
//
// Known Bugs:	(NOVEMBER 4th, 2013) Only known bug...Once clock pulses faster 
//				than 390uS, then can only make narrower, not wider
//
// Tasks to Do:	Change Continuous mode to go from CCW-to-0-to-CW
//
// Last Updated: JUNE 16th, 2014 - 18:00
//
//*****************************************************************************

//*****************************************************************************
//TESTED MOTOR CONFIGURATION:
//
// 1.) Portescap 23H118D10B Stepper Motor 
//		Specs: 1A; 1.8 degree per step (200step per revolution) 
//		Wiring: 24V-Grey-Red-Black-Yellow-Ground
// 2.) Vref => ~1.12V
// 3.) MTH  => ~2.48V
//
//*****************************************************************************

//*****************************************************************************
//	JUMPER SETTINGS
//
// 1.) JUMPER J4 => Jump pin3 to pin4 (Power circuit via USB/LDO: 3.3V)
// 2.) JUMPER J5 => Jump pin3 to pin4 (Power circuit via USB/LDO: 3.3V)
//
//*****************************************************************************

//*****************************************************************************
// Q102 Microcontroller's Hard-wired I/O Pins on the Stepper Motor Driver Board
//
// ================================ ML610Q102 ================================= 
//
// Pin-01 => RESET_N					Pin-16 => "Encoder_Input_CH_A"	- PA0
// Pin-02 => TEST						Pin-15 => "LED_Driver_CLK" 		- PB7
// Pin-03 => "ClkIn_Stepper_CLK" 	- PB0/PWMC	Pin-14 => "+3.3V_C"	 		- VDD
// Pin-04 => "ClkIn_Stepper_CW_CCW"  - PB1	Pin-13 => "GND"		 		- VSS
// Pin-05 => "ClkIn_Stepper_MODE_0"	- PB2		Pin-12 => "LED_Driver_LATCH" 		- PB6
// Pin-06 => "ClkIn_Stepper_MODE_1"	- PB3		Pin-11 => "LED_Driver_SERIN" 		- PB5
// Pin-07 => "Encoder_BUTTON" 	- PA2		Pin-10 => "ClkIn_Stepper_ENABLE"	- PB4 
// Pin-08 => VPP						Pin-09 => "Encoder_Input_CH_B" 	- PA1
//	
// ============================================================================
//
//*****************************************************************************

/*
=== Evaluation Board Objective ===
To allow customers and applications support the ability to evaluate any of Rohm’s BD63720 & BD63876 High 
Performance Stepping Motor Drivers in a quick and easy environment. 

=== Functionality ===
The evaluation board has two drivers installed, the BD63720 Clock-in and the BD63876 Parallel input type. Each
circuit can be connected to a user’s MCU to control the driver and operate the attached stepper motor. Additionally,
the BD63720 circuit can be controlled manually in a single step or continuous mode. 

=== Inputs and Outputs ===
Except for the Circuit Ground, the two circuits on the PCB will be completely separate so as not to back feed or cause
erroneous inputs to the operating circuit. There are four I/O types on the board: Terminal Block (TB), Test Point (TP),
Micro USB (MU) and Header (HDR). Terminal blocks are used to connect to power, ground and the motor. Test Points
are used on all of the I/O signals to allow for easy monitoring with an oscilloscope or meter or to allow quick connection
with a test lead. Header connections are used on the control inputs to allow an easy cable connection to an MCU.

Step Mode 		 Indicates that the step modes can be selected by rotating the knob. 
	Full Step 	 Indicates that the Full Step Mode has been selected for manual mode 
	Half Step A  Indicates that the Half Step A Mode has been selected for manual mode. 
	Half Step B  Indicates that the Half Step B Mode has been selected for manual mode. 
	Quarter Step Indicates that the Quarter Step Mode has been selected for manual mode.

Driver Enabled 	 Indicates that the Manual mode is ready and can be enabled 
(GREEN)		 Indicates that the driver is enabled for Manual mode 

Single Step Mode	 Indicates that the board is prepared to operate in single step mode. 
Continuous 		 Indicates that the board is prepared to operate in continuous mode. 

Pass Through	 Indicates that the Pass-Through mode has been selected 
(GREEN)		 Indicates that the Pass-Through mode is enabled 
*/


/*
BD63720EFV - 36V Extra High-performance & High Reliability Stepper Motor Driver

The BD63720EFV is a bipolar low-consumption driver that
driven by PWM current. Rated power supply voltage of
the device is 36 V, and rated output current is 2.0A.
CLK-IN driving mode is adopted for input interface, and
excitation mode is corresponding to FULL STEP mode,
HALF STEP mode (2 types) and QUARTER STEP
mode via a built-in DAC. In terms of current decay, the
FAST DECAY/SLOW DECAY ratio may be set without
any limitation, and all available modes may be
controlled in the most appropriate way. In addition, the
power supply may be driven by one single system,
which simplifies the design.

MTH 	=> Current decay mode setting terminal (SLOW, MIXED or FAST Decay)
VREF 	=> Output current value setting terminal
CR		=> Terminal to set the Chopping Frequency of output
PS		=> Power Save terminal - can make circuit standby state and make motor output OPEN (when PS=LOW)

*/

//***** START I/O PIN DATA ALIASES *******************************************
//===========================================================================
// I/O PIN DATA ALIASES...
//===========================================================================
	// Connections for Q102 to Control the Stepper Motor IC - ROHM P/N: BD63720EFV  
		#define ClkIn_Stepper_CLK    PB0D	// (pwm_output)
		#define ClkIn_Stepper_CW_CCW PB1D 
		#define ClkIn_Stepper_MODE_0 PB2D 
		#define ClkIn_Stepper_MODE_1 PB3D 
		#define ClkIn_Stepper_ENABLE PB4D

	// Connections for Q102 to Control the LED Driver - ROHM P/N: BD8377FV-M
		#define LED_Driver_SERIN   PB5D 
		#define LED_Driver_LATCH   PB6D
		#define LED_Driver_CLK 	   PB7D

	// Connections for Q102 to Read the Quadrature Encode & Push-Button: 
		#define Encoder_Input_CH_A PA0D 
		#define Encoder_Input_CH_B PA1D 
		#define Encoder_BUTTON	   PA2D

//===========================================================================
//***** END I/O PIN DATA ALIASES *********************************************

//***** START INCLUDE FILES **************************************************
//===========================================================================
// INCLUDED FILES...
//===========================================================================
// Include Path: common;main;irq;timer;clock;tbc;pwm;uart;

	#include	<ML610102.H>	// Lapis Micro ML610Q102 
	#include	<stdlib.h>		// General-purpose utilities
	#include	<stdio.h>		// I/O-related processing
	#include 	<common.h>		// Common Definitions
	#include	<math.h>		// Mathematical functions
	//#include 	<irq.h>			// IRQ Definitions
	//#include 	<mcu.h>			// MCU Definition
	//#include	<ctype.h>		// Character classification and conversion 
	//#include	<errno.h>		// Error identifiers Library
	//#include	<float.h>		// Numerical limits for floating-point numbers
	//#include	<limits.h>		// Numerical limits for integers

	//#include	<muldivu8.h>	// Multiplication and Division accelerator
	//#include	<setjmp.h>		// Global jump (long jump)
	//#include	<signal.h>		// Signal handling functions
	//#include	<stdarg.h>		// Variable numbers of arguments
	//#include	<stddef.h>		// Standard types and macros 

	//#include	<string.h>		// Character string manipulation routines
	//#include	<yfuns.h>		// 
	//#include	<yvals.h>		// Called for by most Header Files
	
	//#include 	<uart.h>		// UART Function Prototypes
	//#include	<i2c.h>			// I2C Definition
	//#include 	<clock.h>		// Set System Clock API
	//#include 	<tbc.h>			// Set TBC (Timer Based Clock) API
	//#include 	<timer.h>		// Timer Macros & APIs
	//#include 	<main.h>		// Clear WDT API
//===========================================================================
//***** END INCLUDE FILES ****************************************************


//***** START FUNCTION PROTOTYPES ********************************************
//===========================================================================
//   FUNCTION PROTOTYPES: 
//	Establishes the name and return type of a function and may specify the 
// 	types, formal parameter names and number of arguments to the function                                 
//===========================================================================
void main (void);
void main_clrWDT( void );			// no return value and no arguments
void Initialization( void );			// no return value and no arguments
void SetOSC( void );				// no return value and no arguments
void PortA_Low( void );				// no return value and no arguments
void PortB_Low( void );				// no return value and no arguments
void PortC_Low( void );				// no return value and no arguments
void PortA_Digital_Inputs( void );		// no return value and no arguments
void PinB0_PWM( void ); 			// no return value and no arguments

void NOPxxx( void );				// no return value and no arguments
void NOPyyy( void );				// no return value and no arguments
void NOP_ClkStep( void );			// no return value and no arguments
void NOP10uS( void );				// no return value and no arguments

void NOP_Long( void );				// no return value and no arguments
void Set_LEDs( void ); 				// no return value and no arguments
void ClockingPulse( void ); 			// no return value and no arguments
void ALL_LEDs_ON( void );			// no return value and no arguments
void ALL_LEDs_OFF( void );			// no return value and no arguments
void myClockingPulse ( void );

void LEDStateA  ( void ); 			// no return value and no arguments
void LEDStateA1 ( void ); 			// no return value and no arguments
void LEDStateA2 ( void ); 			// no return value and no arguments
void LEDStateA3 ( void ); 			// no return value and no arguments
void LEDStateA4 ( void ); 			// no return value and no arguments
void LEDStateB  ( void ); 			// no return value and no arguments
void LEDStateC  ( void ); 			// no return value and no arguments
void LEDStateC1 ( void ); 			// no return value and no arguments
void LEDStateC1A( void ); 			// no return value and no arguments
void LEDStateC2 ( void ); 			// no return value and no arguments
void LEDStateC2A( void ); 			// no return value and no arguments
void LEDStateD  ( void ); 			// no return value and no arguments
void LEDStateE  ( void ); 			// no return value and no arguments

void DisableController( void ); 		// no return value and no arguments
void EnableController( void ); 		// no return value and no arguments
void ButtonKnobCheck ( void ); 		// no return value and no arguments
void EncoderPostion   ( void ); 		// no return value and no arguments
void EncoderDirection ( void );		// no return value and no arguments
void MachineStateAction ( void );		// no return value and no arguments
void ZeroFrequency ( void );			// no return value and no arguments
void GetMode ( void );				// no return value and no arguments

void StepCW (void);				// no return value and no arguments
void StepCCW (void);				// no return value and no arguments
void ContinuousMode(void);			// no return value and no arguments	
void MotorRampUp  (void);			// no return value and no arguments

//===========================================================================
//***** END FUNCTION PROTOTYPES ***********************************************

//***** START GLOBAL VARIABLE DECLARATIONS ************************************
//===========================================================================
//GLOBAL VARIABLE DECLARATIONS......
//===========================================================================
//char char_a;		// -128 to 127
//unsigned char uchar;	// 0-255
//int inta, table [100];	// -32,768 to 32767
//unsigned int uint;	// 0 to 65,535
//long long_a,delay;	// -2,147,483,648 to 2,147,483,647
//float float_a;		// 1.17549435e-38 to 3.40282347e+38
//double double_a;		// 2.2250738585072014e-308 to 1.7976931348623157e+308

//Values for LED Controller Buffer
static char SINGLE_LED,CONTINUOUS_LED,STEP_MODE_LED,PASS_THRU_RED_LED,PASS_THRU_GREEN_LED,DRIVER_EN_RED_LED;
static char DRIVER_EN_GREEN_LED,FULL_STEP_LED, HALF_STEP_A_LED,HALF_STEP_B_LED,QUARTER_STEP_LED,BUFFER_OE_PIN; 
unsigned int mode = 0;						// 0 to 15...										
unsigned int EncoderPosition = 0;			// 1-4 Quadrature Encoder position
unsigned int previous_encoder_position = 0; 	// 1-4 Quadrature Encoder position
unsigned int button_flag = 0;   		// 1 indicates Button was Pressed...
unsigned int AbsolutePosition = 0; 	// 1-4 Quadrature Encoder position  
unsigned int direction = 0;			// 0=NO CHANGE, 1=CW, 2=CCW
unsigned int previousDirection = 0; 	// 0=NO CHANGE, 1=CW, 2=CCW	 
unsigned int Frequency = 0; 			// For CONTINUOUS MODE

//ADJUSTED THESE TWO BELOW VARIABLE 6/16/2014 to work with PORTESCAP 23H118D 10B Stepper Motor.
static unsigned int CWClkPlseWidth  = 4000;  // <=========CHANGE THIS VALUE TO OPTIMIZE!!! (1000=1.83uS; 4000=7.312ms)
static unsigned int CCWClkPlseWidth = 4000;  // <=========CHANGE THIS VALUE TO OPTIMIZE!!! (1000=1.83uS; 4000=7.312ms)
//===========================================================================
//***** END GLOBAL VARIABLE DECLARATIONS **************************************

	

//***** START MAIN FUNCTION **************************************************
//===========================================================================
//  	Start of MAIN FUNCTION
//===========================================================================
void main(void)
{
							
PowerOnReset:
	// Set Q102 micro to desired initial state...
	Initialization(); 		//Oscillator, Ports, UART, Timers, Comparators, LEDs, etc.
	DisableController(); 	//Disable Controller at PowerOn or RESET

Start:
	EncoderPostion();    	//EncoderPosition: 	1-4 Quadrature Encoder position	
	previous_encoder_position = AbsolutePosition; 

MainLoop:
				
	ButtonKnobCheck();  	//Check for BUTTION Press & KNOB Rotation	
	MachineStateAction();	//Act based on Machine State...

goto MainLoop;

}  //END main Function
//===========================================================================
//***** END MAIN FUNCTION *****************************************************



//*****************************************************************************
//===========================================================================
//	Initialize Q102 Micro to Desired State...
//===========================================================================
static void Initialization(void){

	//Initialize Peripherals	
		//BLKCON2 Control Bits...Manually Set 
			DUA0  = 1; 		// 0=> Enables the operation of UART0 (initial value).
	
			BLKCON4 = 0x01; // 0=> Enables SA type ADC
			BLKCON6 = 0x01; // (1=disables; 0=enables) the operation of Timers 8, 9, A, E, F.
			BLKCON7 = 0x01; // (1=disables; 0=enables) the operation of PWM (PWMC)

	// Port Initialize
		PortA_Low();	//Initialize all 3 Ports of Port A to GPIO-Low
		PortB_Low();	//Initialize all 8 Ports of Port B to GPIO-Low

	//Setup Quadrature Encoder Inputs on A0, A1 & A2
		PortA_Digital_Inputs();

	// PWM...	
		//PinB0_PWM();	// Set up PWM Pin on B.0...(PWMC)


	// Comparator...	
		//analog_comparator();

	// Set Oscillator Rate...Must Have.
     		SetOSC();
			
    
	// TTTTTTTTTTTTTTTTTTTTTTTTTTTTTTTTTTTTTTTTTTTTTTTTTTTTTTTTT
	// TIMER SETUP...

	Setup_Timer_8:
	// Reset TIMER DATA REGISTER...
		TM8D    = 0;	//Timer 8 DATA Register

	// Reset TIMER CLOCK REGISTER...
		TM8C    = 0;	//Timer 8 CLOCK Register

	// TIMER-8 Control...
	//   CONTROL-0 Register:
		// Operation Clock for Timer...
		T8C1 = 0;	// 01 = HTBCLK  
		T8C0 = 1;
		// Count Mode...
		T89M16 = 0;	// 0=8-Bit Mode; 1=16bit Mode...
		//One-Shot or Normal Mode...
		T8OST = 0;	// 0=Normal; 1=One-Shot...
	//   CONTROL-1 Register:
		// RUN Mode...
		T8RUN = 0;	//0=STOP; 1=START...

	// TTTTTTTTTTTTTTTTTTTTTTTTTTTTTTTTTTTTTTTTTTTTTTTTTTTTTTTTT


	
	// IIIIIIIIIIIIIIIIIIIIIIIIIIIIIIIIIIIIIIIIIIIIIIIIIIIIIIIII
	// INTERRUPT SETUP...
		//irq_di();	// Disable Interrupts
		//irq_init();	// Initialize Interrupts (All Off and NO Requests)

		// INTERRUPT ENABLE REGISTERS...
		//  IE0 = VOLTAGE LEVEL SUPERVISOR Int.
		//  IE1 = EXTERNAL Ints on B1, B0, A2, A1, & A0
		//  IE2 = SUCCESSIVE APPROXIMATION Int.
		//  IE3 = TIMERS 8 & 9 Ints.
		//  IE4 = UART & COMPARATOR Ints.
		//  IE5 = TIMERS A, B, E & F Ints.
		//  IE6 = PWMC &  128Hz & 32Hz TBC Ints.
		//  IE7 = 16Hz & 2Hz TBC Ints.
		IE0 = IE1 = IE2 = IE3 = IE4 = IE5 = IE6 = IE7 = 0;

		// INTERRUPT REQUEST REGISTERS...
		//  IRQ0 = WDT & VLS Int Requests
		//  IRQ1 = EXTERNAL Int Requests
		//  IRQ2 = SUCCESSIVE APPROXIMATION Int Requests
		//  IRQ3 = TIMERS 8 & 9 Int Requests 
		//  IRQ4 = UART & COMPARATOR Int Requests 
		//  IRQ5 = TIMERS A, B, E & F Int Requests 
		//  IRQ6 = PWMC &  128Hz & 32Hz TBC Int Requests 
		//  IRQ7 = 16Hz & 2Hz TBC Int Requests 
		IRQ0 = IRQ1 = IRQ2 = IRQ3 = IRQ4 = IRQ5 = IRQ6 = IRQ7 = 0;


		E2H = 0; 	// E2H is the Enable flag for 2Hz TBC Interrupt (1=ENABLED)
		
		
		//(void)irq_setHdr( (unsigned char)IRQ_NO_I2C0INT, _intI2c );
		//(void)irq_setHdr( (unsigned char)IRQ_NO_UA1INT, _intUart );
		//(void)irq_setHdr( (unsigned char)IRQ_NO_UA0INT, _intUart );

		//EUA0 = 1; // EUA0 is the enable flag for the UART0 interrupt (1=ENABLED)
		//irq_ei(); // Enable Interrupts
	// IIIIIIIIIIIIIIIIIIIIIIIIIIIIIIIIIIIIIIIIIIIIIIIIIIIIIIIII


	//LLLLLLLLLLLLLLLLLLLLLLLLLLLLLLLLLLLLLLLLLLLLLLLLLLLLLLLLLLLLLLLLLLLLLLLLLLLLLLLL
	//SET LED's & BUFFER_OE to INITIAL STATE...
	//12-bits from output of LED Driver BD8377FV-M (D0-D11):
		STEP_MODE_LED 		= 1; // Bit D2  => "STEP MODE" LED 		(Orange)
	  	FULL_STEP_LED 		= 0; // Bit D7  => "FULL STEP" LED		(YELLOW)
	  	HALF_STEP_A_LED 		= 0; // Bit D8  => "HALF STEP A" LED	(YELLOW)
	  	HALF_STEP_B_LED 		= 0; // Bit D9  => "HALF STEP B" LED	(YELLOW)
	  	QUARTER_STEP_LED 		= 0; // Bit D10 => "QUARTER STEP" LED	(YELLOW)

		DRIVER_EN_RED_LED 	= 0; // Bit D6  => "DRIVER ENABLED" LED  	(RED)
		DRIVER_EN_GREEN_LED	= 0; // Bit D5  => "DRIVER ENABLED" LED 	(GREEN)

	  	SINGLE_LED 			= 0; // Bit D0  => "SINGLE" LED 		(Orange)
	  	CONTINUOUS_LED 		= 0; // Bit D1  => "CONTINUOUS" LED 	(Orange)

		PASS_THRU_GREEN_LED 	= 0; // Bit D3  => "PASS THRU" LED		(GREEN)
		PASS_THRU_RED_LED 	= 0; // Bit D4  => "PASS THRU" LED		(RED)

		BUFFER_OE_PIN 		= 0; // Bit D11 => Octal Buffer_OE

		Set_LEDs();		// Send 12-Bit Data to BD8377 Driver, Clock & Latch
	//LLLLLLLLLLLLLLLLLLLLLLLLLLLLLLLLLLLLLLLLLLLLLLLLLLLLLLLLLLLLLLLLLLLLLLLLLLLLLLLL


		mode = 1; 					//Initialize "mode" to Step-MODE
		direction = 0;				//Initialize "direction" to 0
		AbsolutePosition = 0;		//Initialize "AbsolutePosition " to 0
		button_flag = 0;			//Initialize "button_flag" to 0
		Frequency = 0;				//Initialize "Frequency " to 0

	// WDT...
	WDTMOD = 0x03; 	// 0x03=overflow 8sec...
	main_clrWDT(); 	// Clear WDT
	
} //END Initialization Function
//*****************************************************************************


//*****************************************************************************
//===========================================================================
// 	Clear the Watch-Dog-Timer
//===========================================================================
void main_clrWDT( void )
{
	//How to clear the Watch Dog Timer:
	// => Write alternately 0x5A and 0xA5 into WDTCON register
	do {
		WDTCON = 0x5Au;
	} while (WDP != 1);
	WDTCON = 0xA5u;
} //END main_clrWDT Function
//*****************************************************************************


//*****************************************************************************
//===========================================================================
//	OSC set
//===========================================================================
static void SetOSC(void){

	//FCON0: 			// xMHz PLL (3=1MHz; 2=2MHz; 1=4MHz; 0=8MHz)...
	SYSC0  = 0;			// Used to select the frequency of the HSCLK => 00=8.192MHz.
	SYSC1  = 0;

	OSCM1  = 1;			// 10 => Built-in PLL oscillation mode
	OSCM0  = 0;
   	
	ENOSC  = 1;			// 1=Enable High Speed Oscillator...MUST ENABLE before setting SYSTEM CLOCK!
	SYSCLK = 1;			// 1=HSCLK; 0=LSCLK (MUST set ENOSC = 1 first) 

	LPLL   = 1;			// 1=Enables the use of PLL oscillation - ADDED 4/30/2013

	__EI();			// INT enable
} //END SetOSC Function
//*****************************************************************************


//*****************************************************************************
//===========================================================================
//	Clear All 3 Bits of Port A
//===========================================================================
void PortA_Low(void){

//Carl's Notes...

//Step 1: Set Pin Direction...
//Step 2: Set Pin I/O Type...
//Step 3: Set Pin Purpose...
//Step 4: Set Pin Data...

	//Direction...	
	PA0DIR = 0;		// PortA Bit0 set to Output Mode...
	PA1DIR = 0;		// PortA Bit1 set to Output Mode...
	PA2DIR = 0;		// PortA Bit2 set to Output Mode...

	//I/O Type...
	PA0C1  = 1;		// PortA Bit0 set to CMOS Output...
	PA0C0  = 1;		
	PA1C1  = 1;		// PortA Bit1 set to CMOS Output...
	PA1C0  = 1;	
	PA2C1  = 1;		// PortA Bit2 set to CMOS Output...
	PA2C0  = 1;	

	//Purpose...
	PA0MD1  = 0;	// PortA Bit0 set to General Purpose Output...
	PA0MD0  = 0;	
	PA1MD1  = 0;	// PortA Bit1 set to General Purpose Output...
	PA1MD0  = 0;	
	PA2MD1  = 0;	// PortA Bit2 set to General Purpose Output...
	PA2MD0  = 0;	

	//Data...
	PA0D = 0;		// A.0 Output OFF....
	PA1D = 0;		// A.1 Output OFF....
	PA2D = 0;		// A.2 Output OFF....

}  //END PortA_Low Function
//*****************************************************************************
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

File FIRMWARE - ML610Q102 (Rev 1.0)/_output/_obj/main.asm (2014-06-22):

;; Compile Options : /TML610102 /MS /near /Icommon /Imain /Iirq /Itimer /Iclock /Itbc /SS 64 /SD /Oa /Ot /W 3 /Wc /Fa_output\_obj\ /Zs 
;; Version Number  : Ver.3.41.8
;; File Name       : main.c

	type (ML610102) 
	model small, near
	$$NVARmain segment data 2h #0h
	$$NINITVAR segment data 2h #0h
	$$NINITTAB segment table 2h any
	$$NTABmain segment table 2h #0h
	$$ALL_LEDs_OFF$main segment code 2h #0h
	$$ALL_LEDs_ON$main segment code 2h #0h
	$$ButtonKnobCheck$main segment code 2h #0h
	$$ContinuousMode$main segment code 2h #0h
	$$DisableController$main segment code 2h #0h
	$$EnableController$main segment code 2h #0h
	$$EncoderDirection$main segment code 2h #0h
	$$EncoderPostion$main segment code 2h #0h
	$$Initialization$main segment code 2h #0h
	$$LEDStateA$main segment code 2h #0h
	$$LEDStateA1$main segment code 2h #0h
	$$LEDStateA2$main segment code 2h #0h
	$$LEDStateA3$main segment code 2h #0h
	$$LEDStateA4$main segment code 2h #0h
	$$LEDStateB$main segment code 2h #0h
	$$LEDStateC$main segment code 2h #0h
	$$LEDStateC1$main segment code 2h #0h
	$$LEDStateC1A$main segment code 2h #0h
	$$LEDStateC2$main segment code 2h #0h
	$$LEDStateC2A$main segment code 2h #0h
	$$LEDStateD$main segment code 2h #0h
	$$LEDStateE$main segment code 2h #0h
	$$MachineStateAction$main segment code 2h #0h
	$$MotorRampUp$main segment code 2h #0h
	$$NOP10uS$main segment code 2h #0h
	$$NOP_ClkStep$main segment code 2h #0h
	$$NOP_Long$main segment code 2h #0h
	$$NOPxxx$main segment code 2h #0h
	$$NOPyyy$main segment code 2h #0h
	$$PinB0_PWM$main segment code 2h #0h
	$$PortA_Digital_Inputs$main segment code 2h #0h
	$$PortA_Low$main segment code 2h #0h
	$$PortB_Low$main segment code 2h #0h
	$$SetOSC$main segment code 2h #0h
	$$Set_LEDs$main segment code 2h #0h
	$$StepCCW$main segment code 2h #0h
	$$StepCW$main segment code 2h #0h
	$$ZeroFrequency$main segment code 2h #0h
	$$analog_comparator$main segment code 2h #0h
	$$main$main segment code 2h #0h
	$$main_clrWDT$main segment code 2h #0h
	$$myClockingPulse$main segment code 2h #0h
	$$NTABButtonKnobCheck$main segment table 2h #0h
	$$NTABMachineStateAction$main segment table 2h #0h
	STACKSEG 040h
CVERSION 3.41.8
CGLOBAL 01H 03H 0000H "Set_LEDs" 08H 02H 87H 00H 81H 02H 00H 00H 07H
CGLOBAL 01H 03H 0000H "main_clrWDT" 08H 02H 7AH 00H 80H 00H 00H 00H 07H
CGLOBAL 01H 03H 0000H "NOP_ClkStep" 08H 02H 84H 00H 82H 04H 00H 00H 07H
CGLOBAL 01H 03H 0000H "StepCW" 08H 02H 0A1H 00H 83H 0cH 00H 00H 07H
CGLOBAL 01H 03H 0000H "EnableController" 08H 02H 9AH 00H 80H 00H 00H 00H 07H
CGLOBAL 01H 03H 0000H "EncoderPostion" 08H 02H 9CH 00H 80H 00H 00H 00H 07H
CSGLOBAL 03H 0000H "Initialization" 08H 02H 7BH 00H 81H 02H 00H 00H 07H
CGLOBAL 01H 03H 0000H "PortA_Digital_Inputs" 08H 02H 80H 00H 80H 00H 00H 00H 07H
CGLOBAL 01H 03H 0000H "main" 08H 02H 79H 00H 80H 00H 00H 00H 07H
CGLOBAL 01H 03H 0000H "NOP_Long" 08H 02H 86H 00H 80H 00H 00H 00H 07H
CGLOBAL 01H 03H 0000H "ZeroFrequency" 08H 02H 9FH 00H 80H 00H 00H 00H 07H
CGLOBAL 01H 03H 0000H "ContinuousMode" 08H 02H 0A3H 00H 83H 30H 00H 00H 07H
CSGLOBAL 03H 0000H "SetOSC" 08H 02H 7CH 00H 80H 00H 00H 00H 07H
CGLOBAL 01H 03H 0000H "NOPyyy" 08H 02H 83H 00H 80H 00H 00H 00H 07H
CGLOBAL 01H 03H 0000H "NOPxxx" 08H 02H 82H 00H 80H 00H 00H 00H 07H
CGLOBAL 01H 03H 0000H "NOP10uS" 08H 02H 85H 00H 83H 06H 00H 00H 07H
CGLOBAL 01H 03H 0000H "EncoderDirection" 08H 02H 9DH 00H 81H 02H 00H 00H 07H
CGLOBAL 01H 03H 0000H "ALL_LEDs_ON" 08H 02H 89H 00H 80H 00H 00H 00H 07H
CGLOBAL 01H 03H 0000H "LEDStateA4" 08H 02H 90H 00H 80H 00H 00H 00H 07H
CGLOBAL 01H 03H 0000H "LEDStateC1" 08H 02H 93H 00H 80H 00H 00H 00H 07H
CGLOBAL 01H 03H 0000H "LEDStateC2" 08H 02H 95H 00H 80H 00H 00H 00H 07H
CGLOBAL 01H 03H 0000H "LEDStateA1" 08H 02H 8DH 00H 80H 00H 00H 00H 07H
CGLOBAL 01H 03H 0000H "LEDStateA2" 08H 02H 8EH 00H 80H 00H 00H 00H 07H
CGLOBAL 01H 03H 0000H "LEDStateA3" 08H 02H 8FH 00H 80H 00H 00H 00H 07H
CGLOBAL 01H 03H 0000H "PortB_Low" 08H 02H 7EH 00H 80H 00H 00H 00H 07H
CGLOBAL 01H 03H 0000H "MachineStateAction" 08H 02H 9EH 00H 81H 02H 00H 00H 07H
CGLOBAL 01H 03H 0000H "ALL_LEDs_OFF" 08H 02H 8AH 00H 80H 00H 00H 00H 07H
CGLOBAL 01H 03H 0000H "ButtonKnobCheck" 08H 02H 9BH 00H 81H 02H 00H 00H 07H
CGLOBAL 01H 03H 0000H "StepCCW" 08H 02H 0A2H 00H 83H 0cH 00H 00H 07H
CGLOBAL 01H 03H 0000H "MotorRampUp" 08H 02H 0A4H 00H 82H 08H 00H 00H 07H
CGLOBAL 01H 03H 0000H "PortA_Low" 08H 02H 7DH 00H 80H 00H 00H 00H 07H
CGLOBAL 01H 03H 0000H "DisableController" 08H 02H 99H 00H 80H 00H 00H 00H 07H
CGLOBAL 01H 03H 0000H "analog_comparator" 08H 02H 0AEH 00H 80H 00H 00H 00H 07H
CGLOBAL 01H 03H 0000H "LEDStateC1A" 08H 02H 94H 00H 80H 00H 00H 00H 07H
CGLOBAL 01H 03H 0000H "LEDStateC2A" 08H 02H 96H 00H 80H 00H 00H 00H 07H
CGLOBAL 01H 03H 0000H "LEDStateA" 08H 02H 8CH 00H 80H 00H 00H 00H 07H
CGLOBAL 01H 03H 0000H "LEDStateB" 08H 02H 91H 00H 80H 00H 00H 00H 07H
CGLOBAL 01H 03H 0000H "LEDStateC" 08H 02H 92H 00H 80H 00H 00H 00H 07H
CGLOBAL 01H 03H 0000H "LEDStateD" 08H 02H 97H 00H 80H 00H 00H 00H 07H
CGLOBAL 01H 03H 0000H "LEDStateE" 08H 02H 98H 00H 80H 00H 00H 00H 07H
CGLOBAL 01H 03H 0000H "PinB0_PWM" 08H 02H 81H 00H 80H 00H 00H 00H 07H
CGLOBAL 01H 03H 0000H "myClockingPulse" 08H 02H 8BH 00H 81H 02H 00H 00H 07H
CSTRUCTTAG 0000H 0000H 0004H 000CH 00000016H "_Notag"
CSTRUCTMEM 42H 00000002H 00000000H "_Mode" 02H 00H 08H
CSTRUCTMEM 43H 00000002H 00000002H "_Handle" 02H 00H 08H
CSTRUCTMEM 42H 00000002H 00000004H "_Buf" 04H 03H 00H 00H 00H
CSTRUCTMEM 42H 00000002H 00000006H "_Bend" 04H 03H 00H 00H 00H
CSTRUCTMEM 42H 00000002H 00000008H "_Next" 04H 03H 00H 00H 00H
CSTRUCTMEM 42H 00000002H 0000000AH "_Rend" 04H 03H 00H 00H 00H
CSTRUCTMEM 42H 00000002H 0000000CH "_Rsave" 04H 03H 00H 00H 00H
CSTRUCTMEM 42H 00000002H 0000000EH "_Wend" 04H 03H 00H 00H 00H
CSTRUCTMEM 42H 00000002H 00000010H "_Back" 05H 01H 02H 00H 00H 00H
CSTRUCTMEM 42H 00000001H 00000012H "_Cbuf" 02H 00H 00H
CSTRUCTMEM 42H 00000001H 00000013H "_Nback" 02H 00H 00H
CSTRUCTMEM 43H 00000002H 00000014H "_Tmpnam" 04H 03H 00H 00H 00H
CSTRUCTTAG 0000H 0000H 0003H 0001H 00000004H "_Notag"
CSTRUCTMEM 42H 00000004H 00000000H "_Off" 02H 00H 02H
CSTRUCTTAG 0000H 0000H 0002H 0002H 00000008H "_Notag"
CSTRUCTMEM 43H 00000004H 00000000H "quot" 02H 00H 02H
CSTRUCTMEM 43H 00000004H 00000004H "rem" 02H 00H 02H
CSTRUCTTAG 0000H 0000H 0001H 0002H 00000004H "_Notag"
CSTRUCTMEM 43H 00000002H 00000000H "quot" 02H 00H 01H
CSTRUCTMEM 43H 00000002H 00000002H "rem" 02H 00H 01H
CSTRUCTTAG 0000H 0000H 0000H 0008H 00000001H "_Notag"
CSTRUCTMEM 52H 00000001H 00000000H "b0" 02H 00H 00H
CSTRUCTMEM 52H 00000001H 00000001H "b1" 02H 00H 00H
CSTRUCTMEM 52H 00000001H 00000002H "b2" 02H 00H 00H
CSTRUCTMEM 52H 00000001H 00000003H "b3" 02H 00H 00H
CSTRUCTMEM 52H 00000001H 00000004H "b4" 02H 00H 00H
CSTRUCTMEM 52H 00000001H 00000005H "b5" 02H 00H 00H
CSTRUCTMEM 52H 00000001H 00000006H "b6" 02H 00H 00H
CSTRUCTMEM 52H 00000001H 00000007H "b7" 02H 00H 00H
CUNIONTAG 0000H 0000H 0005H 0002H 00000008H "_Notag"
CUNIONMEM 42H 00000008H "_W" 05H 01H 04H 00H 00H 08H
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

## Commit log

2014-06-22 Stepper Motor Eval Board Control Firmware
    This is the firmware for the LAPIS ML610Q102 mcu that controls the ROHM
    BD63715EFV Stepper Motor Driver IC, as well as the ROHM BD8377 LLED
    Driver, and the logic for the Eval Board
2014-06-25 Stepper Motor Eval Board Project Files Added
    Cleaned old folder, and added full project files
    [DRILL.DRL, L1.GBR, L2.GBR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]
2014-10-17 Updated User Manual & Schematics
    Contains User Manual Version 1.1 & Schematic version 1.0
2014-11-03 Update Documentation
    Updated User Manual to Rev 1.2. Added Getting Started Flyer. Added raw
    images for user manual. Added Bill of Material (B.O.M) for Eval Board.
